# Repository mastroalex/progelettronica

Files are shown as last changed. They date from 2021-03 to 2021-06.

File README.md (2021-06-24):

# Progetto elettronica

## Introduction 
The idea of the project is to show the concept and how to control gripper and rotation via sensor signals. The structure is very simple and made in full of maker and DIY philosophy, only with recycled objects. 
An example in the following figure.

Demonstration: [https://youtu.be/k1hNBbgfAyE](https://youtu.be/k1hNBbgfAyE)

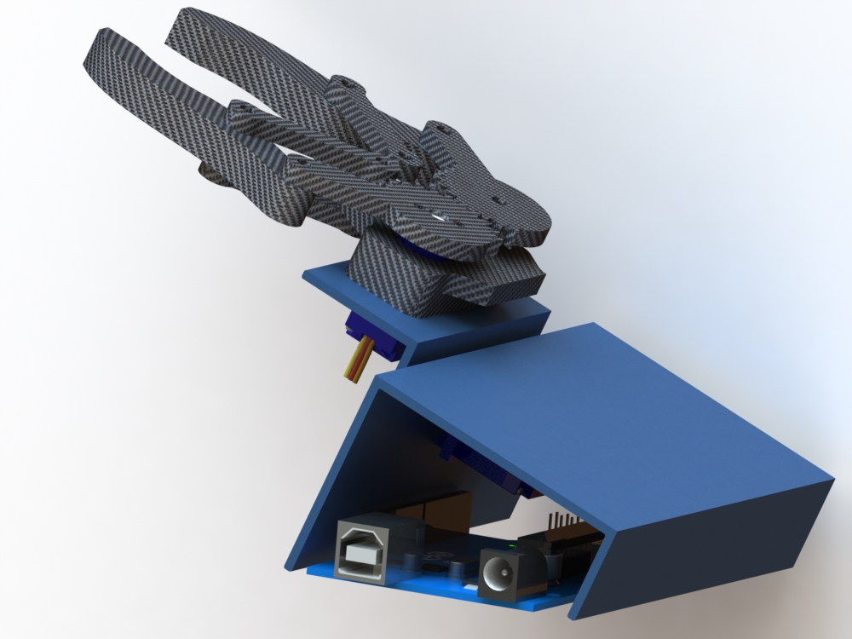
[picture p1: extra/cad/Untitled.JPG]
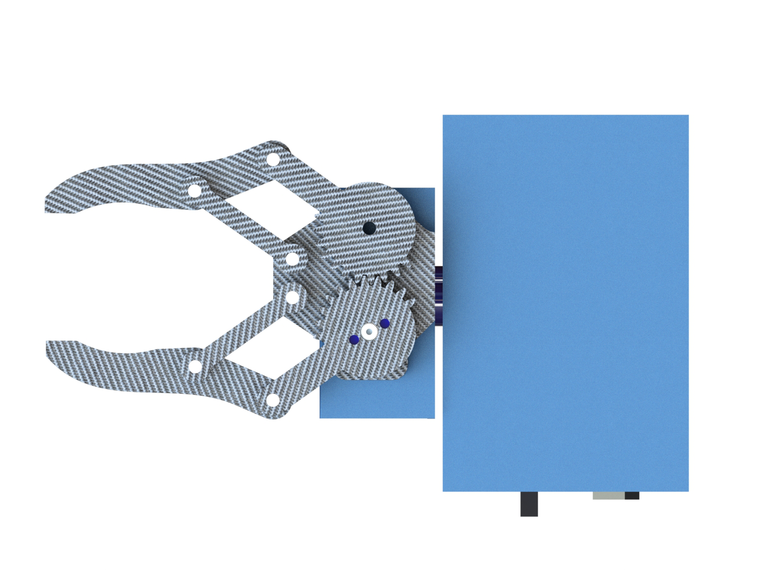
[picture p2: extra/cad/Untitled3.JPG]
  

The gripper has been further simplified in different version but the same project could be realized by purchasing a robot gripper. 

One possibility is to make it with two gears by connecting one to the servomotor. this version involves the use of recycled materials to demonstrate the use of the device.

structure 

For data charts: [bit.ly/datiprogettoelettronica](http://bit.ly/datiprogettoelettronica). 

## Table of contents
- [Progetto elettronica](#progetto-elettronica)
  * [Introduction](#introduction)
  * [Table of contents](#table-of-contents)
  * [Prerequisites](#prerequisites)
  * [Getting started](#getting-started)
    + [GY-521](#gy-521)
    + [Servo](#servo)
    + [EMG Sensor](#emg-sensor)
    + [EMG Electrodes](#emg-electrodes)
    + [Pulse sensor](#pulse-sensor)
    + [DS18B20 Sensor](#ds18b20-sensor)
    + [Sensor testing](#sensor-testing)
  * [Device division](#device-division)
    + [nRF24L01](#nrf24l01)
    + [Arduino Nano for sensing](#arduino-nano-for-sensing)
    + [Arduino Uno for execution](#arduino-uno-for-execution)
  * [GUI](#gui)
    + [Processing and computer app](#processing-and-computer-app)
    + [Python app](#python-app)
    + [Mobile app](#mobile-app)
    + [iOS App](#ios-app)
  * [Data logging and storage](#data-logging-and-storage)
    + [Esp 8266](#esp-8266)
    + [DHT 11](#dht-11)
    + [MySQL Database](#mysql-database)
    + [POST Request](#post-request)
    + [Data visualizing](#data-visualizing)
  * [Make it more compact](#make-it-more-compact)
    + [Sensors cable](#sensors-cable)
    + [Reading station](#reading-station)
    + [Power supply](#power-supply)
  * [Conclusions and future developments](#conclusions-and-future-developments)
  * [References](#references)
  * [Authors](#authors)

## Prerequisites

* Arduino UNO
* Arduino Nano
* GY-521
* EMG Sensor 
* EMG Electrodes
* Microservo motor SG90
* DS18B20 Sensor
* nRF24L01
* HC-05(06)
* ESP8266 Node Mcu
* TTL Converter 3,3-5V
* RJ45 Connectors & Cat5e cable
* LCD Display (I2C)
* Trimmer
* DHT11
_________________

* [MPU6050_tockn](https://github.com/Tockn/MPU6050_tockn) - Arduino library for easy communicating with the MPU6050
* nRF24L01 Library 
* Vectorial graphic software
* DHT Library

* MySQL server
* Web domain 

## Getting started

> Watch: [https://youtu.be/k1hNBbgfAyE](https://youtu.be/k1hNBbgfAyE)

### GY-521 
GY-521 is a module that manages the MPU-6050 sensor, a chip manufactured by Invensense, which is a IMU (Inertia Measurement Unit) sensor based on MEMS technology that contains a three-axis accelerometer and a three-axis gyroscope embedded in a single chip. This is a 6 DOF (degrees of freedom) IMU sensor so it gives six values as output. It also contains a temperature sensor.

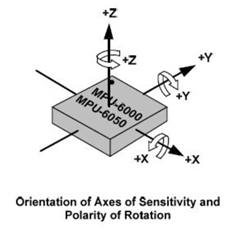
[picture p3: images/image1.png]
orientation_of_axes


The accelerometer is capable of detecting the angle of inclination along the three axes, while the gyroscope detects the angular velocity around the three axes.
GY-521 module is small in size but it is very accurate, it contains a 16-bit analog to digital conversion hardware for each channel so it captures the x, y, and z channel at the same time.
The sensor uses the I2C protocol for communication.
Two libraries are required one for the I2C and the other for communicating with MPU-6050.
 ```c
 #include <MPU6050_tockn.h>
 MPU6050 mpu6050(Wire);
 #include <Wire.h>
 ```

### Servo 
A servomotor is a rotary actuator or linear actuator that allows for precise control of angular or linear position, velocity and acceleration. It consists of a suitable motor coupled to a sensor for position feedback. It also requires a relatively sophisticated controller, often a dedicated module designed specifically for use with servomotors.

Microservo SG90 is used. It can rotate approximately 180 degrees (90 in each direction) and works just like the standard kinds but smaller.

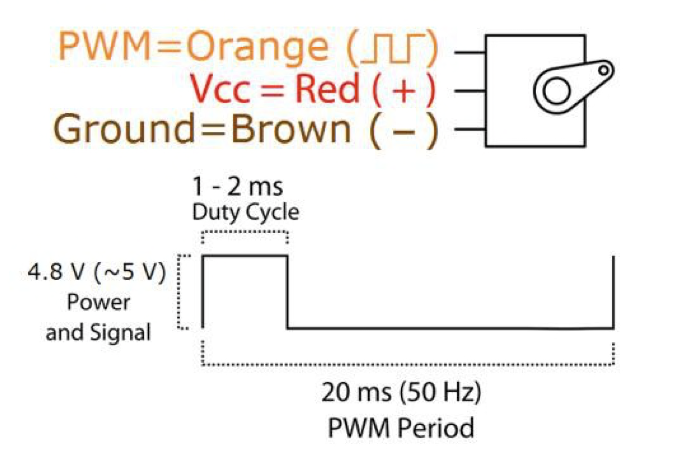
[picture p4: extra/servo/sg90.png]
servo_control


Position "0" (1.5 ms pulse) is middle, "90" (~2ms pulse) is middle, is all the way to the right, "-90" (~1ms pulse) is all the way to the left.
The Servo library is used to control the servo motor.
 ```c
#include <Servo.h> 
Servo servo-object-name;
```

Then use the following command to control angle from 0 to 180 degrees.

 ```c
servo-object-name.write(degrees);
```
The following diagram includes the connection for both the servo and the IMU.

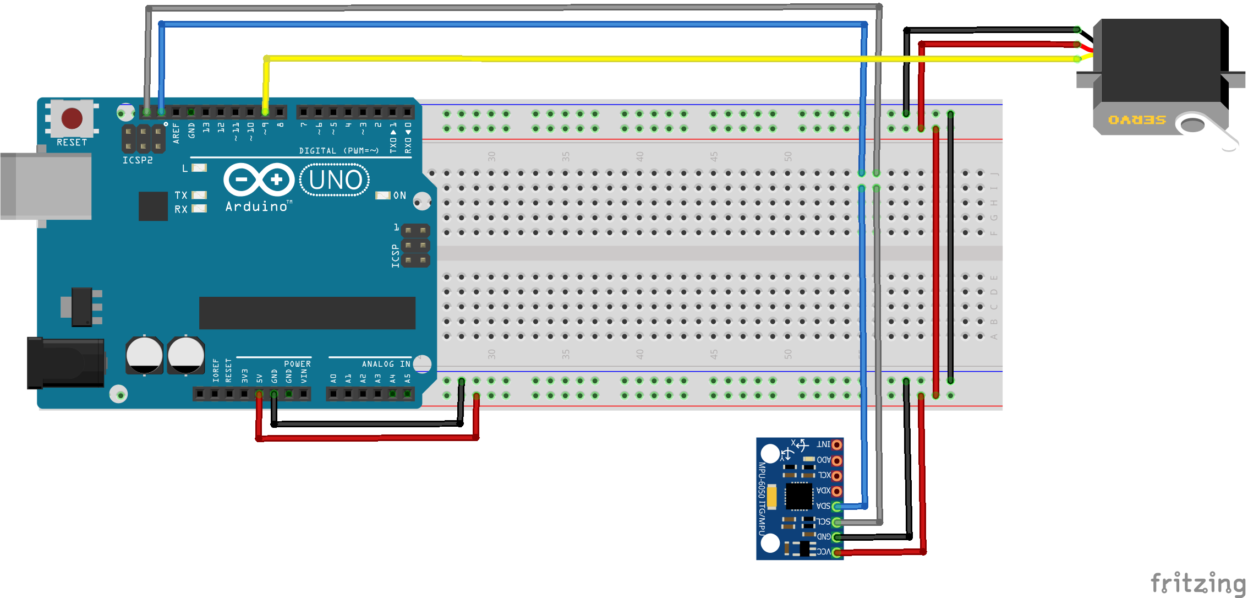
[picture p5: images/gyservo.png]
servo+gy


### EMG Sensor
EMG (Electromyography) sensor is able to measure a muscle's activity by monitoring the electric potential generated by muscle cells, electromyography has traditionally been used for medical research and diagnosis of neuromuscular disorders, however now EMG sensors are used in robotics and other control systems. It evaluates the health condition of muscles and the nerve cells that control them. These nerve cells are known as motor neurons. They transmit electrical signals that cause muscles to contract and relax. An EMG translates these signals into graphs or numbers, helping doctors to make a diagnosis.
This sensor amplifies and processes the electric activity of a muscle and converts it into an analog signal which can be read by any microcontroller with an analog-to-digital converter like Arduino.
When the muscle under test flexes, the sensors's output voltage increses.

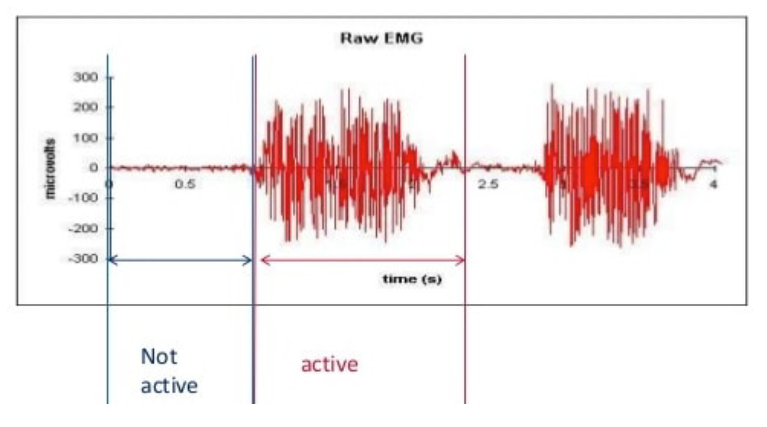
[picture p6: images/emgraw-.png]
emgraw


Linked to the sensor via 3,5 mm jack connector there is a cable which is connected on one side to Arduino, while on the other side ends with three snap connectors 
that attach to three electrodes.

Muscle Sensor v3 is used. It needs a positive and negative reference voltage so two 9V batteries are required.

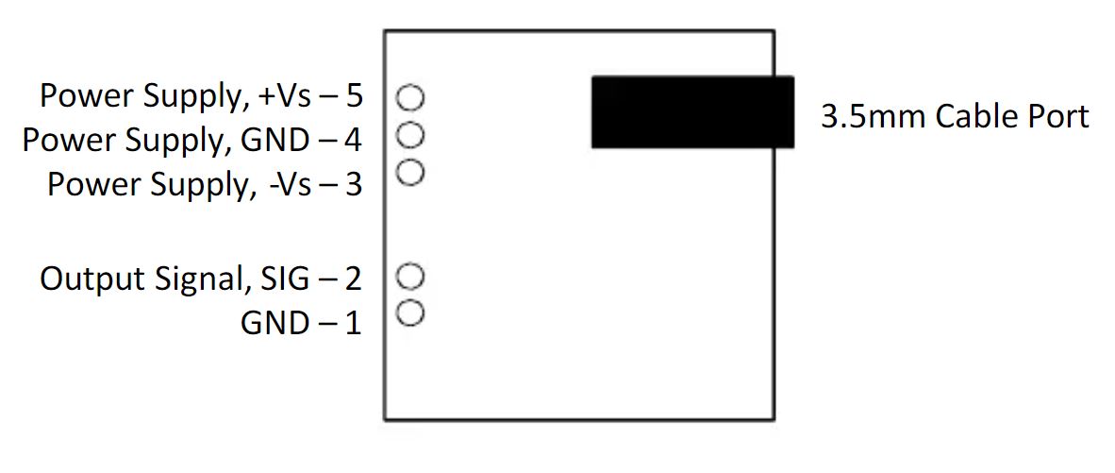
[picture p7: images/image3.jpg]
muscle_sensor


Surface EMG can be recorded by a pair of electrodes or by a more complex array of multiple
electrodes. More than one electrode is needed because EMG recordings display the potential
difference between two separate electrodes.

As you can read in the datasheet or in schematic, the two electrodes signal enter into an amplifier for instrumentation: 

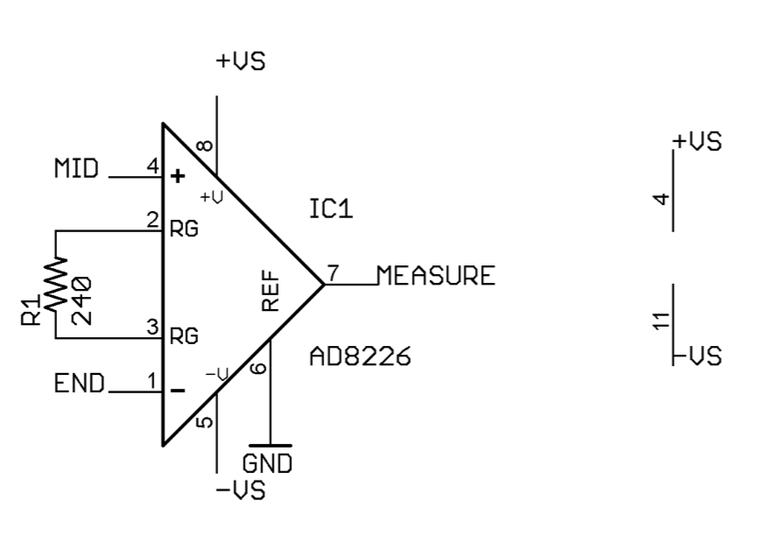
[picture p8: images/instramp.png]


Subsequently the signal is rectified:

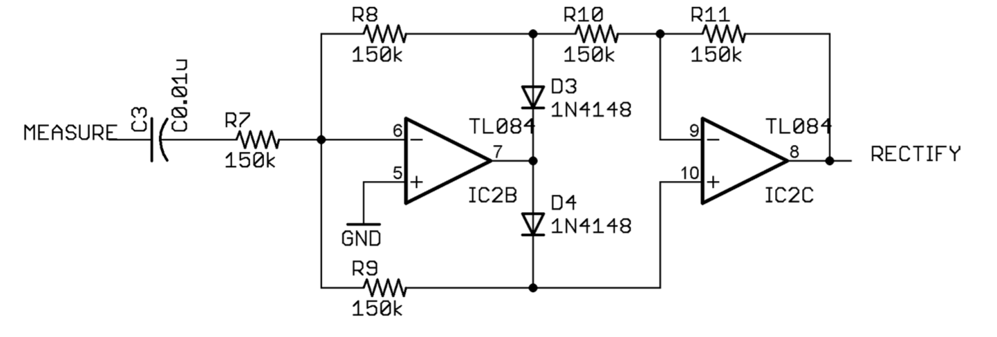
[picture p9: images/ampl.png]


And finally it is smoothed:

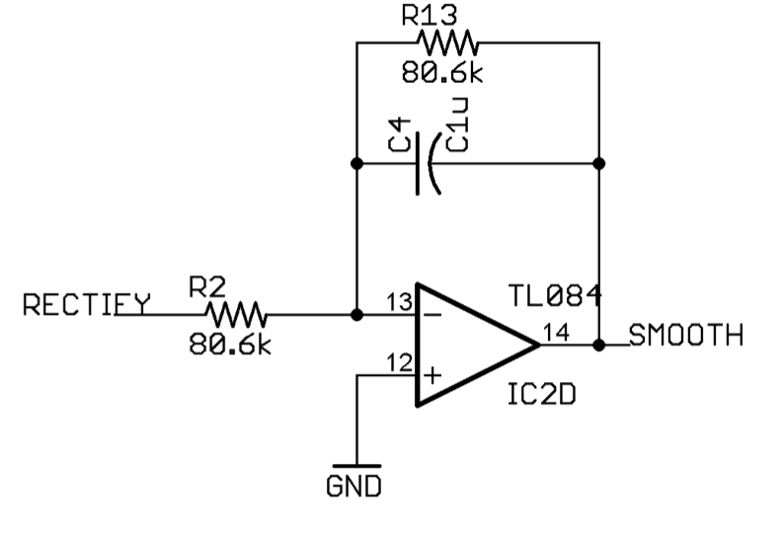
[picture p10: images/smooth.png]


In summary we will have a variable signal with muscle contraction that will be sent to the Arduino A/D converter.

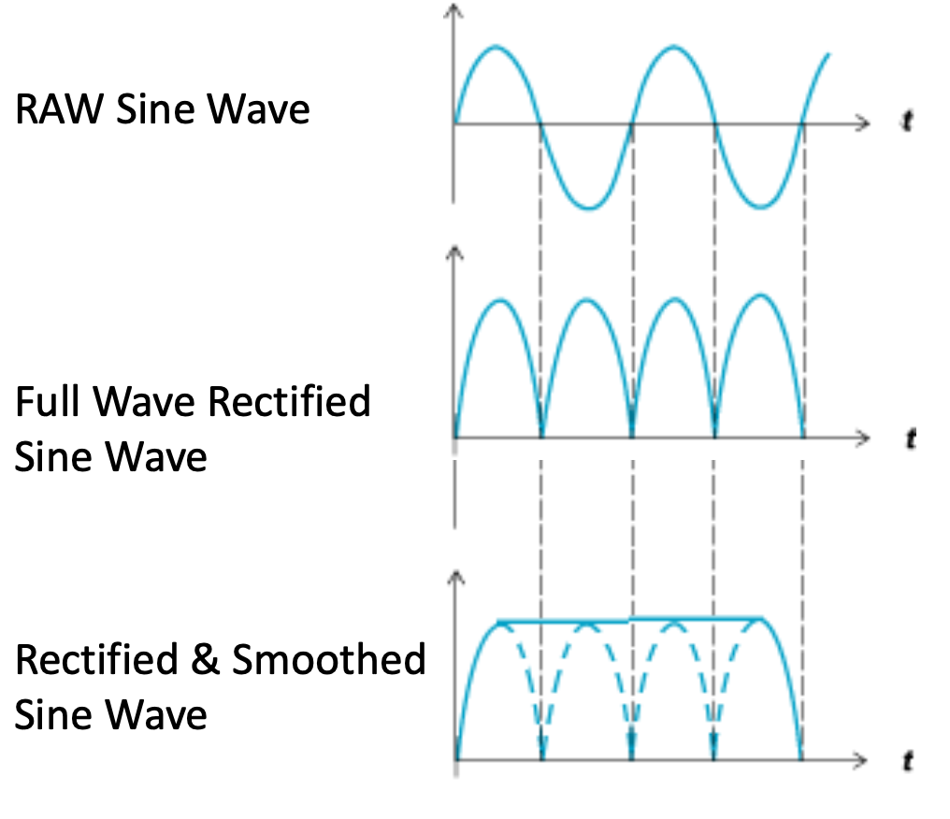
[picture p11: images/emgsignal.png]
emgsignal


The muscelsensor V3 is discontinued so we have chosen a copy. This copy of the V3 allows a considerable saving however it has some defects. This sensor outputs a signal without smoothing and full of disturbs.

We also made a vectorial copy (`.svg`) that you can include in fritzing to easily draw the following schemes. This requires respecting the [fritzing standards](https://fritzing.org/learning/tutorials/creating-custom-parts) to design own parts. For more informations [this guide](https://learn.sparkfun.com/tutorials/make-your-own-fritzing-parts/all).

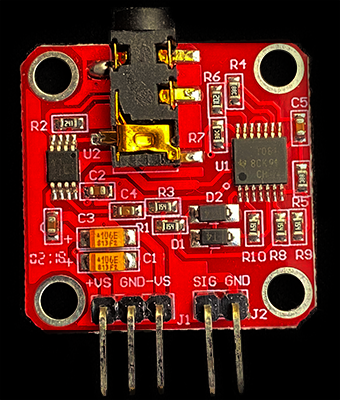
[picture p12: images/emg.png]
emg
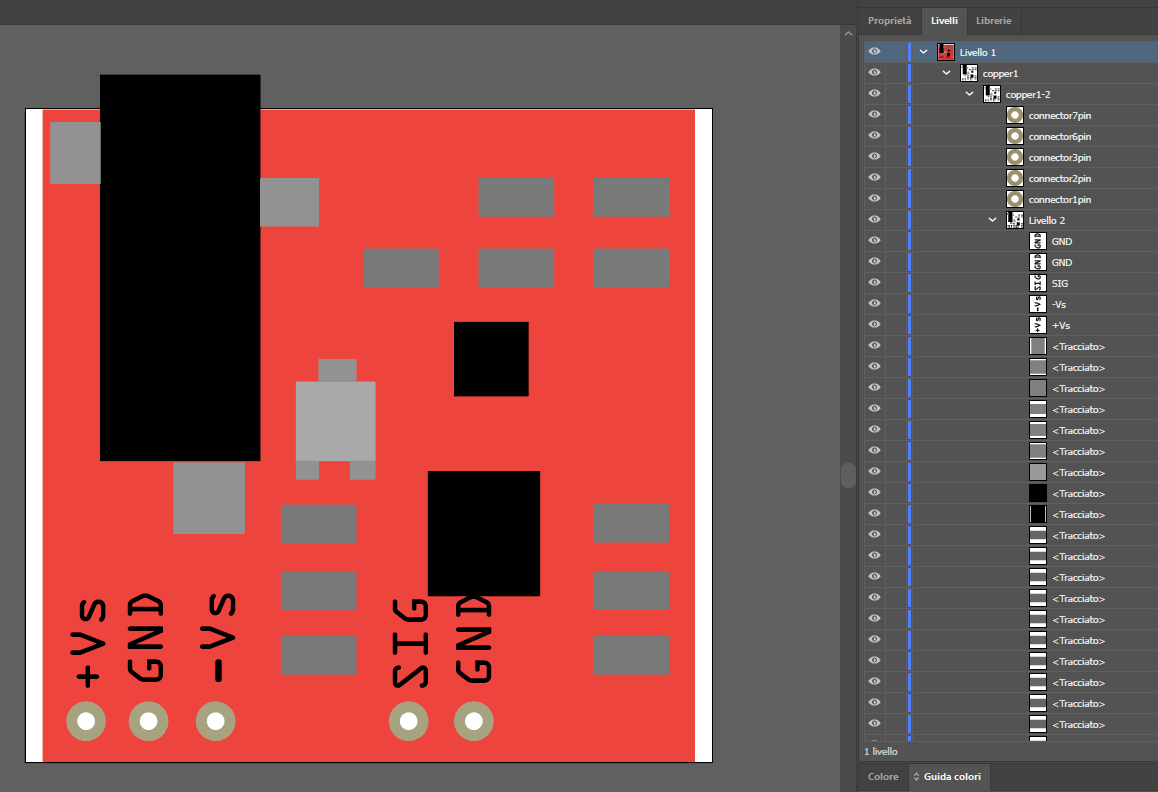
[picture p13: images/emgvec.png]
emg2
 

### EMG Electrodes
The electrical activity of a muscle is detected with the help of EMG electrodes. There are differente types of electrodes, surface EMG electrodes are used in this project, in particular the gelled one.
This type of elecrodes contains a gelled electrolytic substance as interface between electrodes and skin. 
Gelled EMG electrodes provide a non invasive technique for measurements and detection of EMG signal, but they are generally used for superficial muscles since they are applied on the skin. 
The EMG electrodes must be positioned appropriately. In particular two EMG electrodes should be placed between the motor unit and the tendinous insertion of the muscle, along the longitudinal midline of the muscle. The distance between the center of the two electrodes should be 1-2 cm. Red snap connector in the middle of muscle body and the green one at one end of the muscle body. 
The third electrode (yellow one) must be placed on an inactive section of the body.

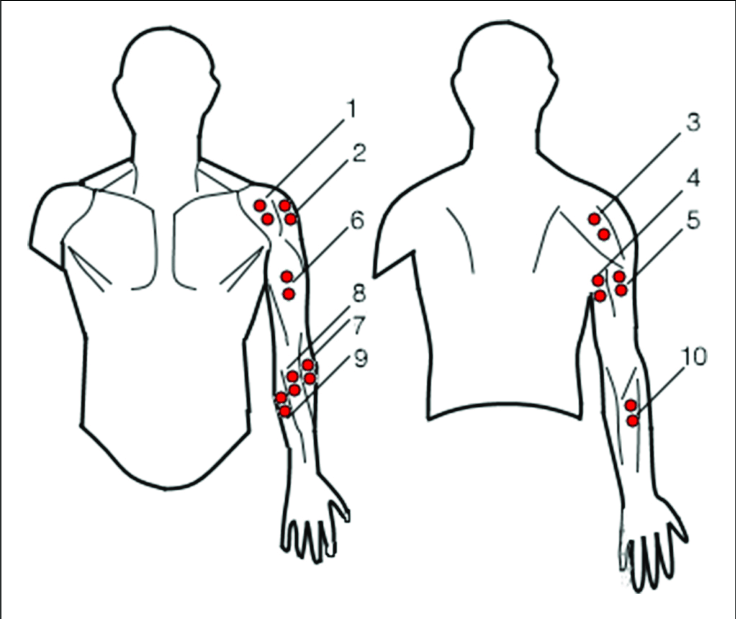
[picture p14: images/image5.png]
electrodes_placement


It is also important to do some considerations about emg signals.

The electrical source is the muscle membrane potential of about –90 mV. 
Typical repetition rate of muscle motor unit firing is about 7–20 Hz, depending on the size of the muscle
Measured EMG potentials range between less than 50 μV and up to 30 mV, depending on the muscle under observation. 
**It must be amplified !**

Due to the low quality of the emg circuit the analog signal was full of noise. The voltage was only rectified but not very leveled. So we provided to simple smoothing algorithm.

```c

int readings[numReadings];      // the readings from the analog input
int readIndex = 0;              // the index of the current reading
int total = 0;                  // the running total
int average = 0;                // the average
int inputPin = A0;              // EMG analog pin

void setup() {
    Serial.begin(9600);
  // initialize all the readings to 0:
  for (int thisReading = 0; thisReading < numReadings; thisReading++) {
    readings[thisReading] = 0;
  }
}

void loop() {
 
  total = total - readings[readIndex];          // subtract the last reading:
  readings[readIndex] = analogRead(inputPin);   // read from the sensor
  total = total + readings[readIndex];          // add the reading to the total:
  readIndex = readIndex + 1;                    // advance to the next position in the array:

  if (readIndex >= numReadings) {               // if we're at the end of the array
    readIndex = 0;                              // wrap around to the beginning
  }
  average = total / numReadings;                // calculate the average:
                                                // print different data for plotting
  Serial.print(average);
  Serial.print("\t");
  Serial.print(soglia);
  Serial.print("\t");
  Serial.println(analogRead(inputPin));
  delay(1);                                     // delay in between reads for stability
}
 ```

 This is the [Arduino's reference smoothing scritp](https://www.arduino.cc/en/Tutorial/BuiltInExamples/Smoothing/) with little changes made after a long period of testing.

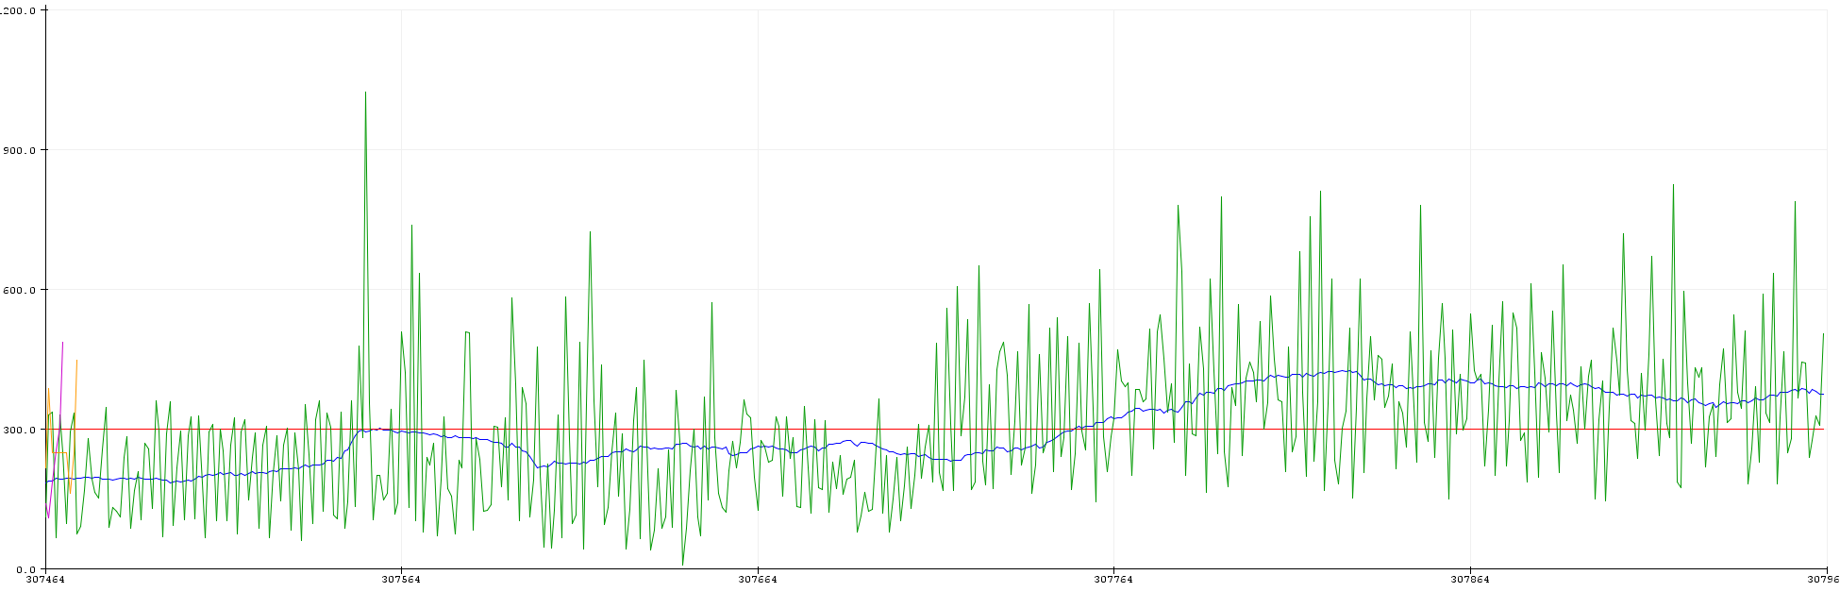
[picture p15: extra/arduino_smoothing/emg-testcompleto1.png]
smoothing
 

 > Smoothed signal (blue), original signal (green), threeshold (red). When the signal is below the threshold the arm is relaxed otherwise it is contracted.

 This smoothed `average` allows us to customize the following control code for the clamp servo.

 ```c
#include <Servo.h>
Servo servoclamp;
long t3 = 0;
long t4 = 20;
boolean controllo[10];
boolean stato;
int i = 0;
int soglia = 350; // Threeshold
// This value derives from a long period of testing. 
// You will need to do several tests 
void setup() {
  servoclamp.attach(5);
    // other code...
  }
 void loop() {
// other code..
  if (average > soglia) {
    servoclamp.write(max_servo_angle);// gripper closing
  }
  if (millis() - t3 < t4) {
    if (average < soglia) {
      controllo[i] = LOW;
    }
    else {
      controllo[i] = HIGH;
    }
    if (i < 10) {
      i++;
    }
    t3 = millis();
  }
    // only if the average is below the threshold
    // for a long time is it possible to close the clamp 
    // this allows to avoid problems due to sudden oscillations of the signal
  for (int j = 0; j < 10; j++) {      
    if (controllo[j] == LOW) {      
      stato = LOW;
    }
    else {
      stato = HIGH;
    }
  }
  if (stato == LOW) {
    servoclamp.write(min_servo_angle);   // gripper opening
  }
 }
 ```

### Pulse sensor 

The principle is to make a light shine between your fingers. Most of the light is absorbed or reflected, but some light will pass through our tissues if they are thin enough. When blood is pumped through your body, it gets squeezed into the capillary tissues, and the volume of those tissues increases very slightly. Then, between heart beats, the volume decreases. The change in volume effects the amount of light that will transmit through. This fluctuation is very small, but we can sense it with electronics. Here's how it's done.

We start with a light source and a light detector. Using an Infrared LED, and a photodiode sensor. It's important that the two devices are matched well, so that the light wavelength output from the LED is detected strongly by the photodiode (see below for part numbers). The photodiode is essentially a teeny tiny solar cell, just like the panels on rooftops, but really small. It will generate a small voltage and current when it is blasted with photons. The Infrared LED is what we will use for our photon blaster.

The next thing we need is a way to amplify the tiny signal coming off of the photodiode. Happily enough, the configuration of this circuit is well-known  as a 'Current to Voltage Converter' and it is a classic.

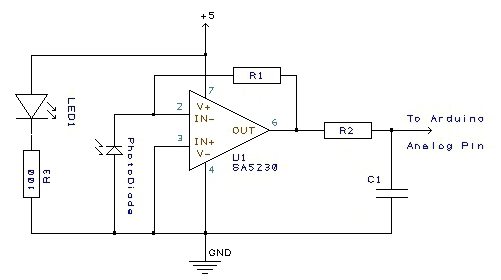
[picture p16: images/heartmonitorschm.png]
heartmonitorschm


The photodiode needs to be shielded from ambient light, which generates alot of noise in the signal. 
The waveform here is usable, but as you can see, the pulse signal is distorted by even small movements. Also any misalignment or movement of the IR LED will muddy up the signal.

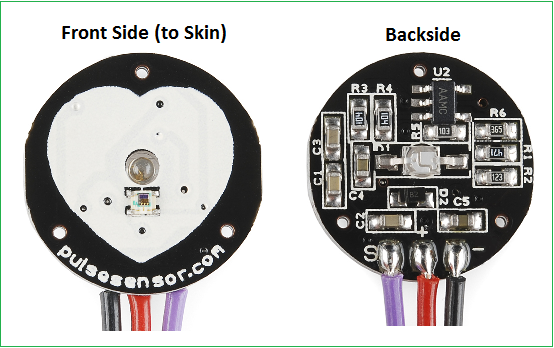
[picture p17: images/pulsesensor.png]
pulse


pulsesensor.com make a Pulse Sensor that is small enough to be worn comfortably in many configurations, and immune to signal noise generated by moving around, or changes in ambient lighting conditions.
They found a super small integrated circuit that has an on-board photodiode and op amp circuit combined. The super smallness means that we can maintain close, steady contact with the skin. This shields the sensor from changes in ambient light and makes noise from moving around minimal at most. 

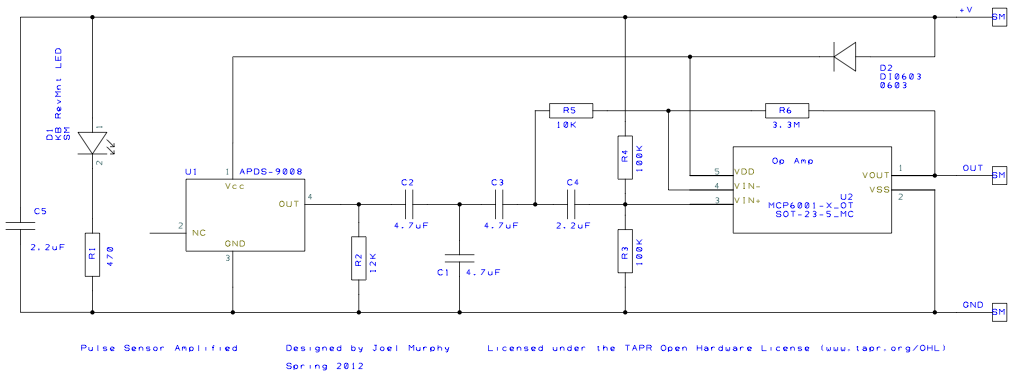
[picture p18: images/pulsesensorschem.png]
pulsesensorschem


The raw signal looks like:

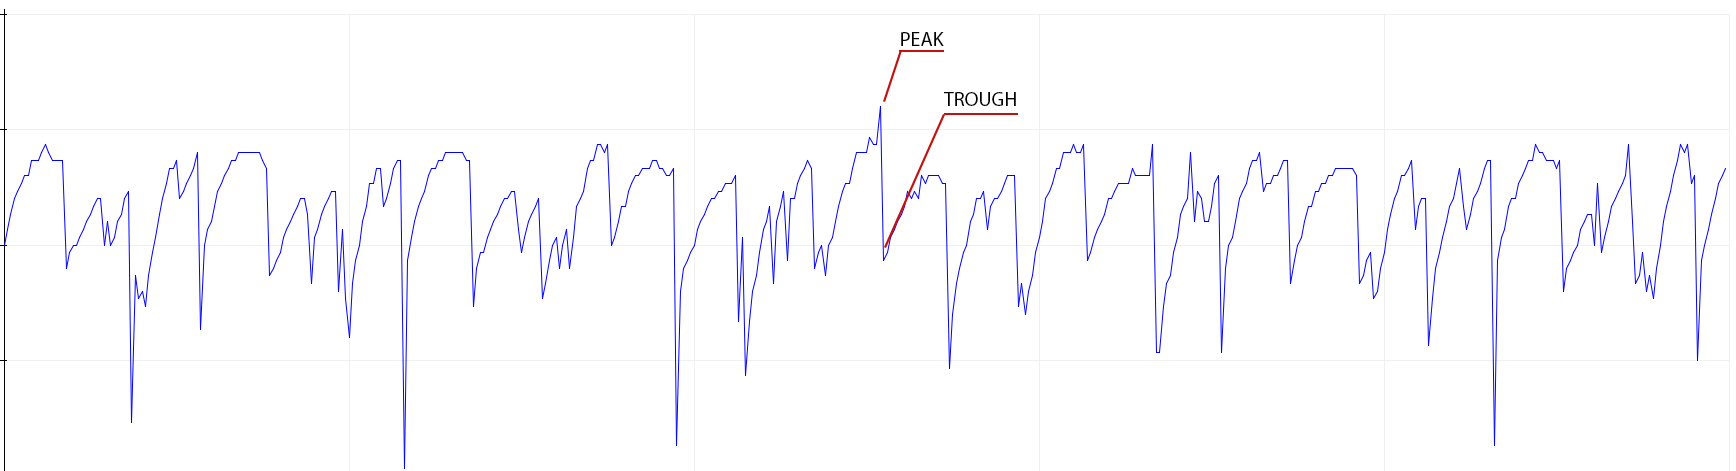
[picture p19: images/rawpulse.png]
rawpulse


A first possibility is to use the library provided `PulseSensor Playground` , however this is not fully compatible with the other features we want to implement. So we proceeded to write a special code. 

Reading is callback by `battiti()` function described in the library `funzioniBPM.h`.

We have therefore put together several ideas from [instructables.com](https://www.instructables.com/circuits/howto/pulse+sensor/) and from [pulsesensor.com](https://github.com/WorldFamousElectronics/PulseSensor_Amped_Arduino/blob/master/PulseSensorAmped_Arduino_1.5.0/PulseSensorAmped_Arduino_1.5.0.ino) to obtain a code that takes care of reading the analog value and identifying the beat above a certain threshold. The code is relatively complex. 
Besides a part to print symbols or an affirmative sentence when the beat is actually detected.
Timer 2 is used to set an interrupt every 2 ms. a more complex piece of code takes care of measuring the time elapsed since the last beat and making appropriate samples to avoid noise. In particular, an attempt is made to avoid dichrotic noise and to reveal peaks. When a beat is detected (peak in compliance with the imposed conditions) the time value is updated and the BPM is calculated as well as the number of beats that can occur in 1 minute (60000 ms).

The main functions are performed by `ISR(TIMER2_COMPA_vect)` and `battiti()` and `serialOutputWhenBeatHappens()` take care of returning the beat values. 

### DS18B20 Sensor
DS18B20 is a digital temperature sensor, which is a sensor capable of measuring the temperature of the environment but also of the ground or to detect temperature in liquids. 
This sensor is available in several sizes, in this project it has been used the one inserted into a waterproof probe. The DS18B20 sensor is much more sensitive than the DHT11 
(temperature and humidity sensor) because it can reach 9 to 12 bit resolution. More with this module it is possibile to add multiple sensors on the same bus, each 
DS18B20 has a unique 64-bit serial code, which allows multiple DS18B20s to function on the same bus.
The protocol used is OneWire protocol which uses a digital pin, from which a bus starts and allows us to communicate with a specific device on the bus knowing the address.

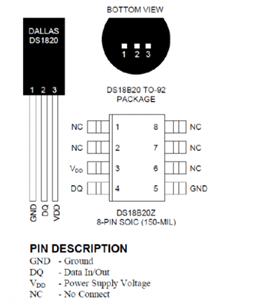
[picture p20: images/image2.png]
temperature_sensor


Two libraries are required, the first one is the DallasTemperature and the second one is the OneWire library. 

 ```c
#include <DallasTemperature.h>
#include <OneWire.h>
```

The DS18B20 was then discontinued due to an incompatibility of the library interrupts and the other functions. The temperature of the GY-521 was deemed to be sufficiently accurate.

### Sensor testing 

The following circuit shows the test setup for developing the initial code:

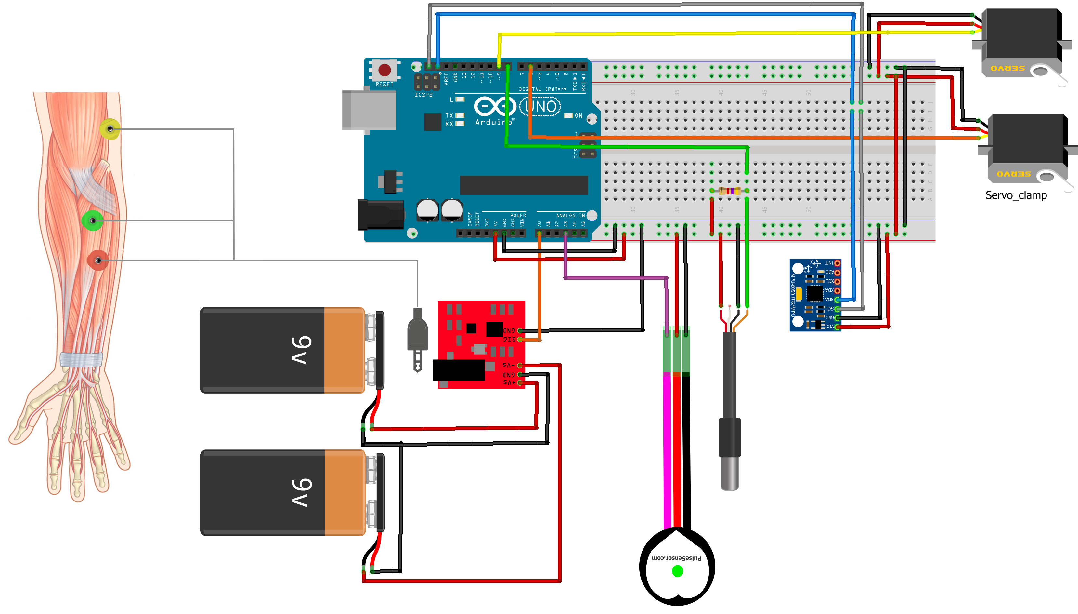
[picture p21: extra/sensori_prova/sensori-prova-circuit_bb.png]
sensor_testing


This configuration of two 9V DC power supplies allows you to have +9 and -9 on the Vs terminals.
It is also possible to use 18V DC power supply and split it in +9V and -9V.

This configuration allowed us to do all the device and code tests. We therefore reworked part of the code by dividing it into the various modules in order to have a more modular system that would allow you to add or remove devices as needed.
From this configuration we started to divide then into a structure determined for monitoring and a structure with actuators.

In the end the sensors that must arrive on the wrist will be joined in a single cable equipped with a connector to connect it to the monitoring structure. 

Everything will be reorganized in a more compact way

## Device division

At this point we have divided the code and the devices. We use an arduino nano to read the sensors and an arduino uno to control the servo motors.

Communication between the two is via radio using two NRF24L01 Single chip 2.4 GHz Transceiver.

### nRF24L01

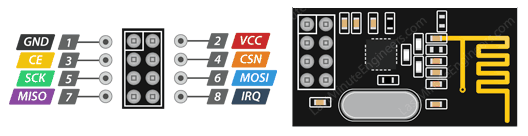
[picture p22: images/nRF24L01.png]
nrf24


The device has an operating voltage of 1.9V ~ 3.6V, a built-in 2,4GHZ antenna and an operating speed (max) of 2 Mbps. 
The chip is managed by the SPI interface. Through this interface it is possible to access the registers of the chip and modify all its parameters.

This complex operation, however, is facilitated for us by libraries.

```c
#include <SPI.h>
#include <nRF24L01.h>
#include <RF24.h>
```

The connection requires several pins:
	
- GND
- Vcc, powers the module  using 3.3V
- CE, Chip Enable, used to enable SPI communication
- CSN, Ship Select Not, pin has to be kept high always, else it will disable the SPI
- SCK,Serial Clock, provides the clock pulse using which the SPI communication works
- MOSI. Master Out Slave In, Connected to MOSI pin of Arduino, for the module to receive data from the arduino
- MISO, Master In Slave Out,Connected to MISO pin of Arduino, for the module to send data from the Arduino
- IRQ, it is an active low pin and is used only if interrupt is required

To use the chip it is necessary to set reading or writing in `setup()`like:

```c
  radio.begin();
  radio.openWritingPipe(address); //for receiving 
//radio.openWritingPipe(address); // for trasmitting
  radio.setPALevel(RF24_PA_MIN);
  radio.stopListening(); //for receiving 
//radio.stopListening();// for trasmitting
```

It is also important to define Chip Enable `CE`and Ship Select Not `CSN`

For the transmission we used a function `charfortransmission()` created ad hoc that allows to concatenate a letter which indicates which data we are transmitting and the value assumed from the corresponding variable. this function is cycled in the `loop()` and continuously called by sending it different parameters depending on the variable. It is then converted into `char` to allow correct transmission with the libraries it uses. 
The receiver has a similar function `radionuovo()` that first analyzes the first character identifying what information is received and then enters the data in the variables of interest, after making the appropriate variable type conversions

### Arduino Nano for sensing 

> Configuration with Arduino nano and sensors on breadboard for testing

nanosensor

For the arduino dedicated to sensors, the circuit has been modified by adding an LCD display to monitor the parameters and an nRF24L01 for radio transmission. The LCD display is connected with an I2C interface module to simplify communication and cable management. The connection of the sensors has remained the same. The DS18B20 sensor has been temporarily excluded due to incompatibility between the libraries. We will decide later whether to include it again by changing the code. So the temperature of the GY-512 is used although not as accurate.

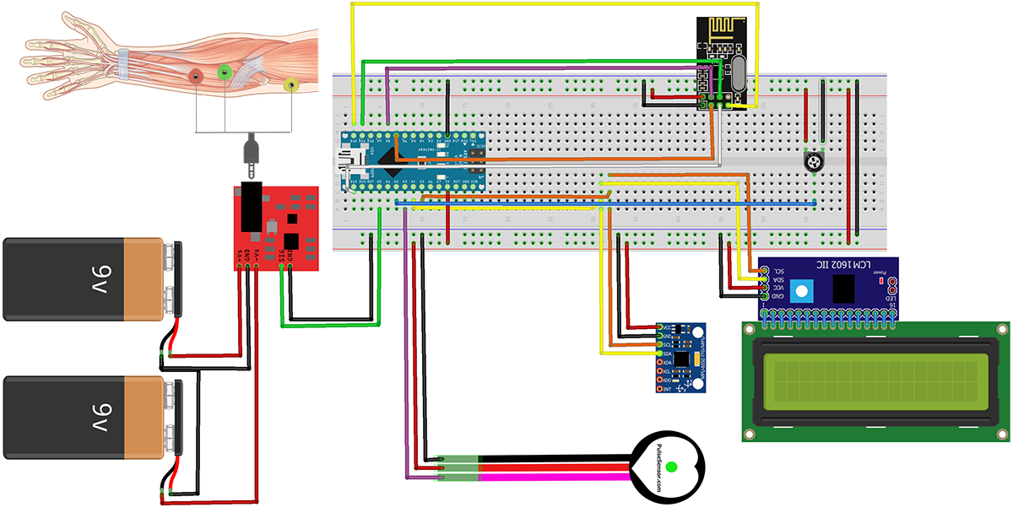
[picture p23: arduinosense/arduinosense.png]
arduinosense


An arduino nano was used to make the whole thing more compact. The pin definition remains the same. It is important to remember that there are no dedicated SDa and SCL pins but they are on A4 and A5.

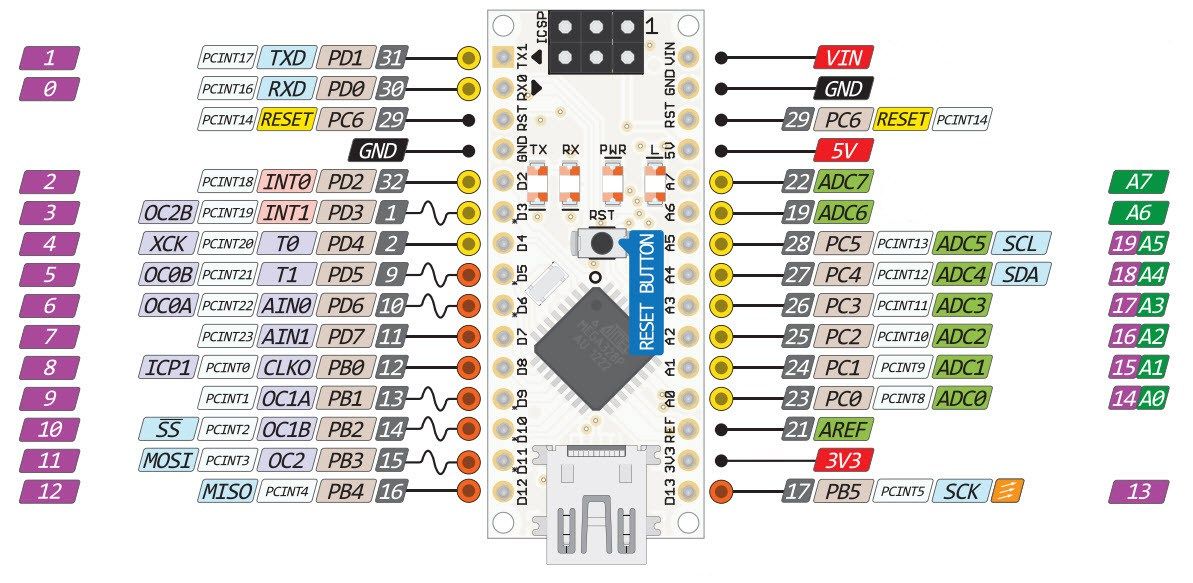
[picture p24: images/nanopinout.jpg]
nanopinout


In the code the elements related to the servo motors have been removed and the rest has been rearranged.

The main code is as follows:

```c
#include <MPU6050_tockn.h>
#include <Wire.h>
#include "funzioniBPM.h" // battiti
#include "printerfunzioni.h" // stampante
#include "EMGsmooth.h" // lettura emg
MPU6050 mpu6050(Wire);
void setup() {
  Serial.begin(9600);
  Wire.begin(); // avvio e inizializzo il gyro
  mpu6050.begin();
  mpu6050.calcGyroOffsets(true);
  // mpu6050.setGyroOffsets(0, 0, 0);
  for (int thisReading = 0; thisReading < numReadings; thisReading++) {  // initialize all the readings to 0:
    readings[thisReading] = 0;
  }
  t1 = millis();
  interruptSetup();                 // sets up to read Pulse Sensor signal every 2mS
  lcd.begin(); // initialize the LCD
  lcd.backlight();
}
void loop() {
  average = averagecalc (); // calcolo media EMG
  mpu6050.update();
  tempmpu = mpu6050.getTemp(); // prende la temperatura
  angle = mpu6050.getAngleX(); // prende l'angolo lungo x
  printatore(LOW); // set HIGH to debug EMG with serial plotter
  lcdprint();
  battiti();
  charfortransmission("T", String(tempmpu));
  charfortransmission("A", String(angle));
  charfortransmission("M", String(average));
  charfortransmission("B", String(BPM));
  charfortransmission("S", String(soglia));
  delay(1);
}
```

This main code has been simplified by adding several functions that call external library definitions:
- ` averagecalc() ` has been defined in the `EMGsmooth.h` and is used to calculate the average of the distorted EMG signal
- `printatore(LOW)` it is a special function that can be used to print the EMG signal for the serial plotter in order to debug any problems with the detection. It is usually used to print all values on the serial monitor. It is defined in `printerfunzioni.h`
- `lcdprint()` it is used to print the different values and connected symbols on the LCD display
- `battiti()`it is used to reveal heartbeats and BPM. It has been defined in the `funzioniBPM.h`
- `charfotransmission()`to trasmitting data with relative informations

To maintain the code clear this function was defined in external libraries. 
The `EMGsmooth.h` library it's responsible of smoothing emg signal in order to obtain precision in threshold determination.
The `funzioniBPM.h` library has already been described in the pulse sensor paragraph.
The `printerfunzioni.h` contains the function to print in the serial monitor and in the lcd display. It also contains the definition of the LCD symbol as an arrow or heart.

To create special characters for LCD it is used  [LCD Custom Generator](https://maxpromer.github.io/LCD-Character-Creator/) that allow us to generate a byte custom char with pixel ON/OFF definition. This allows us to use special symbols in addition to ASCII characters by individually defining the on and off pixels in an 5x8 matrix (`byte_matrix`). It is possible to create up to 8 different symbols with the `createChar ()` function of the LiquidCrystal library and print them with `lcd.Write()`. For example for heart symbol:

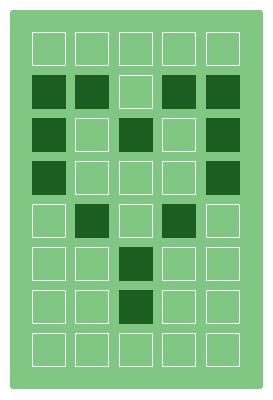
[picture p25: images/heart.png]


```
byte heart[] = {
  B00000,
  B11011,
  B10101,
  B10001,
  B01010,
  B00100,
  B00100,
  B00000
};
lcd.createChar(1, heart);
lcd.setCursor(6, 0);
lcd.write(1);
```

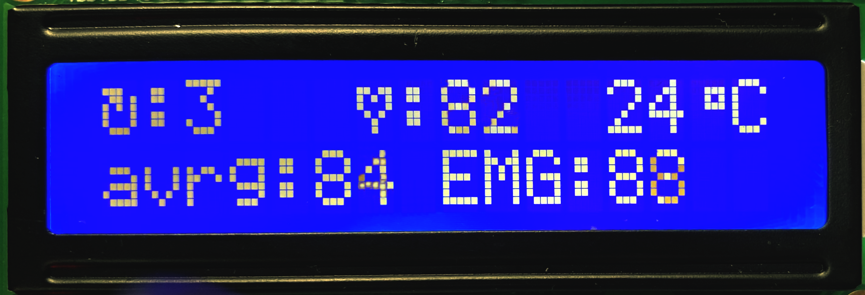
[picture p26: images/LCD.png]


Each library contains all the variables and all the other libraries necessary for their operation. 

We are therefore able to obtain the following values which must be contained to the arduino with the actuators:

- `tempmpu`
- `angle`
- `average`
- `BPM`
- `soglia`

Finally, a trimmer was also added to manually adjust the threshold on the analog pin A2.

### Arduino Uno for execution

> Configuration with Arduino Uno, servomotors, radio trasmitter and clamp  for testing

actuator

This second structure takes care of receiving the radio signals and retransmitting them via bluetooth (or via serial) and to move the two servomotors.
It is important to note that a logic level converter (3.3V 5V TTL) was used to add the bluetooth module.

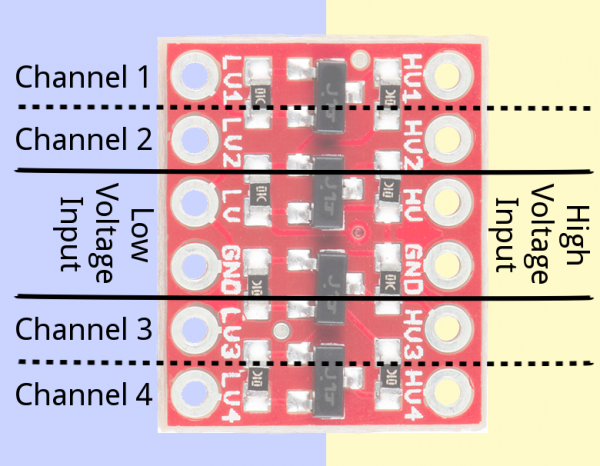
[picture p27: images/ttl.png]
ttl


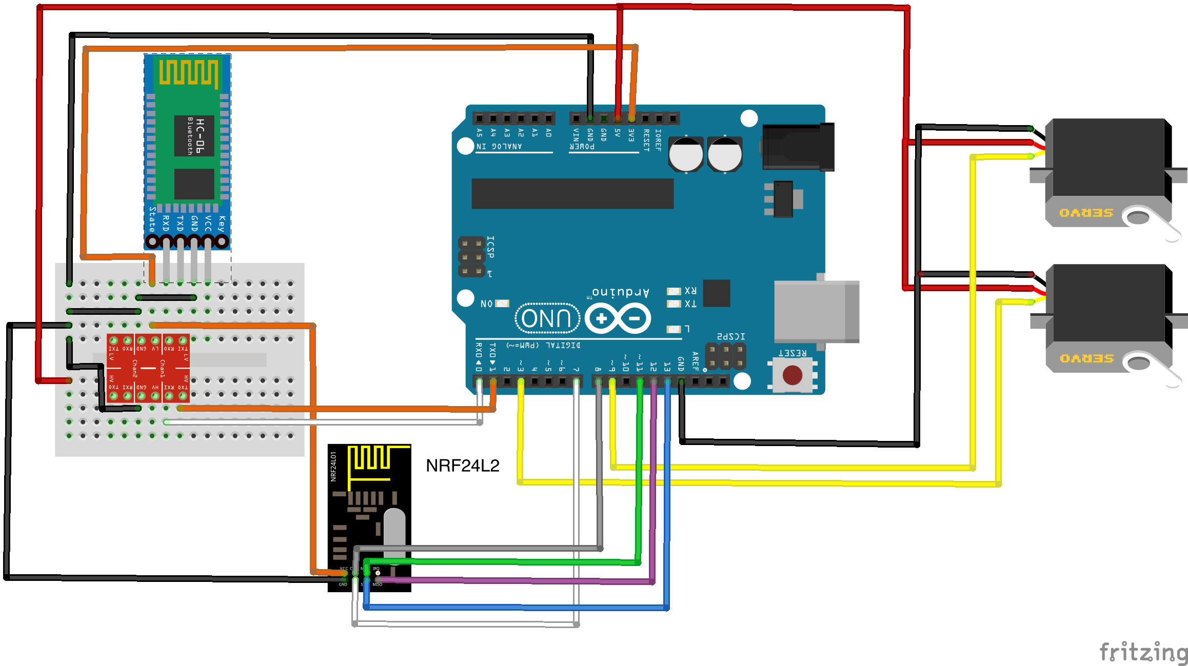
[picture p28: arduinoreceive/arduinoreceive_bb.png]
arduinoreceive


#### HC-06 for bluetooth

The hc-06 module is a device that allows you to transform a signal on the serial bus into a bluetooth signal. 

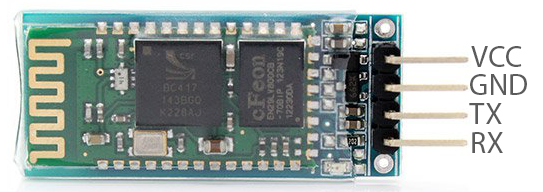
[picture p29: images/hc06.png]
hc06


Typically is used a software serial protocol to communicate however we use directly the UART bus on pin tx and rx.
So we created two new functions `radioperbt()` and `decodeserial()`.
The first one analyzes the char received from the nRF24 and according to the first letter updates the respective variable and at the same time prints the value encoded in the serial (so also in bluetooth).
The second one instead deals with analyzing the commands received. Therefore whether manual control is active or not and, if necessary, the rotation angles of the servomotors. It will be better described in the GUI section.

`radioperbt ()` was originally written as a function to decode the radio message and update variables (`radionuov ()`). Then it has been updated in order to allow bluetooth communication by sending the message encoded with the first letter that indicates which variable corresponds to the data.
```c
if (text[0] == 'T') {
      Serial.print("T");
      valore = "";
      for (int i = 1; i < 32; i++) {
        valore = valore + String(text[i]);
      }
      tempmpu = valore.toFloat();
      Serial.println(tempmpu);
    }
```
The logic is to receive an `array chart`, analyze the first char and convert all the others to the variable of interest (`float` or `int`) and print the message again as a encoded `String`.

#### Servo motors

Two functions have been created to control the servomotors.

`pos_servo()` to which we pass the inclination and takes care of remapping it correctly to rotate the structure.

`pinzacontrol()` which takes care of deciding whether or not to close the clamp according to the threshold value. There is a further check before reopening the clamp to avoid problems due to signal fluctuations.
```c
if (average > soglia) {
    servopinza.write(pinzamax);// chiudo la pinza
  }
if (millis() - t3 > t4) {
  if (average < soglia) {
    controllo[i] = LOW;
  }
  else {
    controllo[i] = HIGH;
  }
  if (i < 10) {
    i++;
  }
  t3 = millis();
  }
for (int j = 0; j < 10; j++) {
  if (controllo[j] == LOW) {
    stato = LOW;
  }
  else {
    stato = HIGH;
  }
}
if (stato == LOW) {
  servopinza.write(pinzamin);// apriamo la pinza
}
  
```

## GUI

We also found it useful to develop a graphical user interface that allow you to view data or take control of the clamp, both from a computer and from a smartphone.

### Processing and computer app

To develop computer app we use Processing, compatible with MacOs, Windows and Linux.

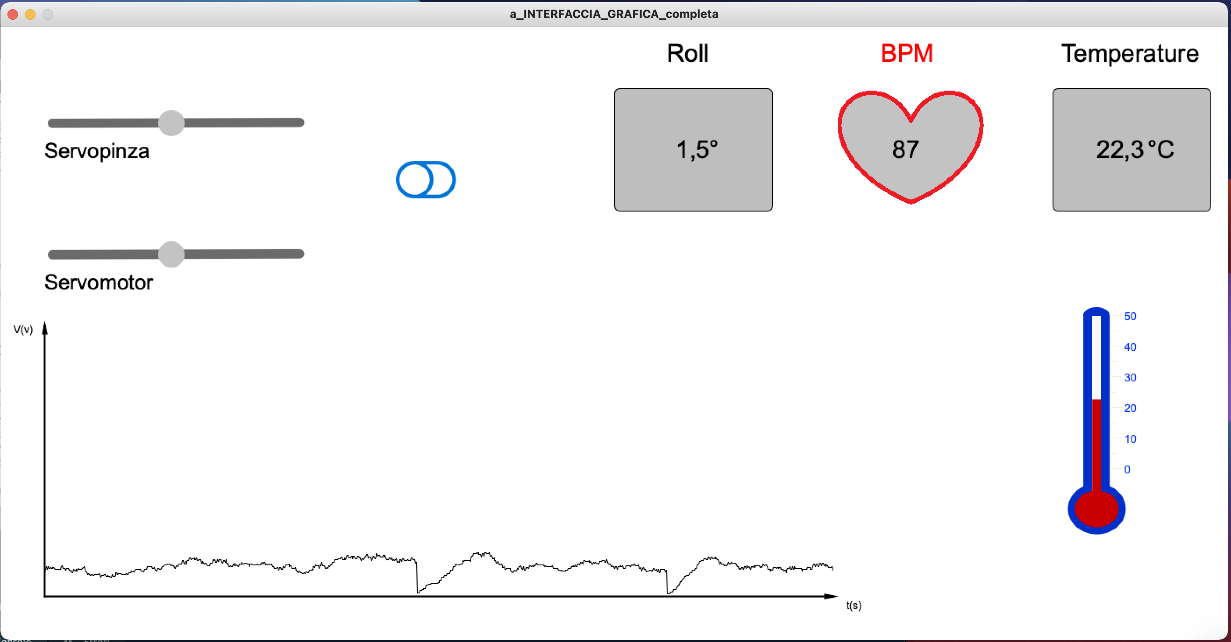
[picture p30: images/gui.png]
gui


#### Sliders

In order to control the clamp and the other servo used in this project two sliders have been created on Processing. 
The first sketch created was the one on Arduino, in particular we have used a library which is called Firmata. Firmata is a library that implements the Firmata protocol for standard communication, to make Arduino or more generally a hardware device communicate with various types of peripherals or programs. 
In this project it was used to make Arduino at the service of an external software that is Processing itself. 
In the example section of the Arduino IDE we called ServoFrimata which is one of the example programs that supports as many servos as possible using the Servo library. 
Once the example was opened, it was compiled and uploaded to Arduino. This meant that Arduino could be interfaced by using this comunication protocol with any other software, program o device with the same protocol like Processing.

The code is as follows:

```c
#include <Servo.h>
#include <Firmata.h>

Servo servos[MAX_SERVOS];
byte servoPinMap[TOTAL_PINS];
byte servoCount = 0;

void analogWriteCallback(byte pin, int value)
{
  if (IS_PIN_DIGITAL(pin)) {
    servos[servoPinMap[pin]].write(value);
  }
}

void systemResetCallback()
{
  servoCount = 0;
}

void setup()
{
  byte pin;
  Firmata.setFirmwareVersion(FIRMATA_FIRMWARE_MAJOR_VERSION, FIRMATA_FIRMWARE_MINOR_VERSION);
  Firmata.attach(ANALOG_MESSAGE, analogWriteCallback);
  Firmata.attach(SYSTEM_RESET, systemResetCallback);
  Firmata.begin(9600);
  systemResetCallback();
  // attach servos from first digital pin up to max number of
  // servos supported for the board
  for (pin = 0; pin < TOTAL_PINS; pin++) {
    if (IS_PIN_DIGITAL(pin)) {
      if (servoCount < MAX_SERVOS) {
        servoPinMap[pin] = servoCount;
        servos[servoPinMap[pin]].attach(PIN_TO_DIGITAL(pin));
        servoCount++;
      }
    }
  }
}

void loop()
{
  while (Firmata.available())
    Firmata.processInput();
}
```

In order to use the Firmata protocol on Processing, besides the serial library which is present by default on Arduino, it is necessary to import a library provided by Arduino which includes an Arduino equivalent software object, which represents the physical arduino connected via USB cable to the computer.

```js
import processing.serial.*;
import cc.arduino.*;
Arduino arduino;
Serial serial;
```

No dedicated libraries have been loaded to create the sliders. In fact the elements that create the slider have been drawn with another program and then added as images inside the program folder.

The images were then loaded into the code in this way:

```js
  barra1 = loadImage("barra1.png");
  indicatore1 = loadImage("indicatore1.png");
  barra2 = loadImage("barra2.png");
  indicatore2 = loadImage("indicatore2.png");
```
And than the images were placed on the window:

```js
  image(barra1, x1, y1);
  image(indicatore1, x2, y2);
  image(barra2, x1, y3);
  image(indicatore2, x4, y4);
```

So when the mouse moves along the x coordinate for the length of the slider in the upper half of the graphic window, the symbol which represents the indicator, will follow the mouse simulating the function of the slider. 
While when the muose moves along the x coordinate for the lenght of the slidere in the lower half of the graphic window, the indicator of the second slider will follow the mouse.
Then according to the position of the mouse the `servoWrite` function writes a value to the servo telling to go to the corresponding angle ranging from 0 to 180 degrees.

The code is as follows:

```js
...
if (mousePressed && mouseY < y1+20) {
      float targetX1 = constrain(mouseX, 100, 380);
      float dx = targetX1 - x2;
      x2 += dx * easing;
      arduino.servoWrite(5, constrain(mouseX / 2, 0, 180));
  }
 if (mousePressed && mouseY > y4-10) {
      float targetX2 = constrain(mouseX, 100, 380);
      float dx = targetX2 - x4;
      x4 += dx * easing;
      arduino.servoWrite(9, constrain(mouseX / 2, 0, 180));
  }
  ```
 
 Below the graphic window with the created sliders:
  
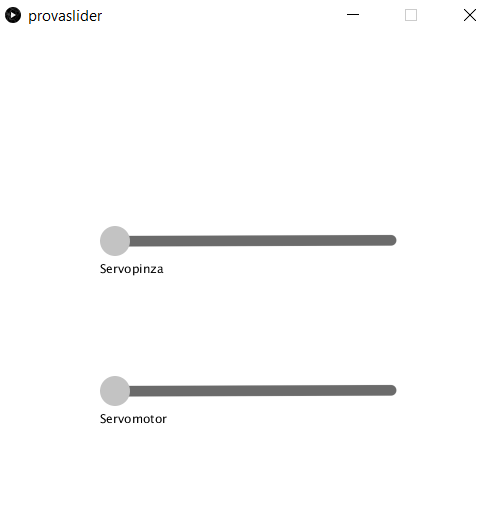
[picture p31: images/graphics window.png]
slider
  
  
#### Graphic

In order to view the data coming from the EMG we have created a graph on Processing in which we can see the trend recorded by the EMG.
To improve the code we have created multiple classes, so that the main sketch is more compact. For the graph we have `public class Grafico`.
to build the graph the axes were drawn first, by using the function `line(x1, y1, x2, y2)`, the values contained inside indicate the position in which the graph has been placed and also the length of the x and y axes which represents respectively the time t(s) and the amplitude V of the oscillations of the EMG.

Inside `public void setdat()` we define an array of 1000 elements and through a for cycle we have access to the element of the array which are the values from the EMG remapped between 0 and 300 (which corresponds to the height of the y axis). Then we define another array which contans as much element as the previous one, again we access to the elements through a for cycle and we define a float variable called `passo` which is the length of the x axis divided by the float variable `data.lenght`. So the value assumed by the elements of the `datax[i]` array is 50 + i * passo.
the code is as follows:

```js
public class Grafico {
public float[] datax; 
 public Grafico(){}
 
 public void setdati(){
 data = new float[1000];
  for (int i=0; i < data.length; i++) {
    data[i] = 100;
  }
  datax = new float[data.length];
  for (int i=0; i < datax.length; i++) {
    float passo=900/float(data.length);
    datax[i] = 50+i*passo;
  }
 }
```  
So once we have defined the relationship between the data received and the x axis we can draw the line which allows us to view the trend of the values detected by the EMG with `line(datax[i], 650-data[i], datax[i+1], 650-data[i+1])`. Once the curve reaches the end of the x axis restart from the origin. 
The direction of the axes indicated by the tip of an arrow and have been created with the triangle function in which the six values represents the position of the three vertices of the triangle.

```js
public void assi(){
 for (int i=0; i<data.length-1; i++) {
    fill(55, 200, 50);
    line(datax[i], 650-data[i], datax[i+1], 650-data[i+1]);
  }

  stroke(0, 0, 250);
  strokeWeight(2);
  //line(50,800-V,950,800-V);
  stroke(0, 0, 0);
  line(50, 350, 50, 650);
  line(50, 650, 950, 650);
  fill(0, 0, 0);
  triangle(48, 350, 52, 350, 50, 340);
  triangle(940, 648, 940, 652, 950, 650);
  textSize(12);
  text("t(s)", 965, 665);
  text("V(v)", 15, 350);
 }
``` 
#### Icon

The icon was added in order to switch the command so that it is possible to control the clamp with the sliders. The switch allows us to switch to manual control. In order to create the switch we have used the Cp5 library which contains the switch among the examples.
it was therefore necessary to import the library:

```js
import controlP5.*;
ControlP5 cp5;
``` 
In the `public class Serialcomunication extends Grafico` we created a function `serialsend()` in which if the manual control is active (`if (pulsante == true)`) and if the mouse is pressed and it is in correspondence with one of the sliders, we can open-close the gripper or rotate it by mapping the position on the slider in the range between 0° and 180° for the gripper and between -90° and 90° for the rotation. Then this value is written as String together with an identification character to the serial port.
the code is as follows:

```js
...

 void serialsend() {
    if (mousePressed) {
      if (millis()-ti>500) {
        if (pulsante==true) {
          if (mousePressed && mouseY < y2+20) {
            float pinzamap=map(target1, 50, 350, 0, 180);
            String pinza="P"+str(pinzamap);
            MyPort.write(pinza);
            println(pinza);
          }
        }

        ti=millis();
      }
      if (millis()-ti2>500) {
        if (pulsante==true) {
          if (mousePressed && mouseY > y4-20) {
            float rotazmap=map(target2, 50, 350, -90, 90);
            String rotaz="R"+ str(rotazmap);
            MyPort.write(rotaz);
            println(rotaz);
          }
        }
        ti2=millis();
      }
    }
  }
  ...
  
``` 
If we click on the icon which has the value “false” by default we give the value `true` and the string `"C1"` is sent on the serial, otherwise if the value is `false` the string `"C0"` is sent on the serial. When the string `"C1"` is read from the serial the boolean variable `controlloapp` is seto to 1 so that the movements of the gripper will be managed by the sliders. 
Instead if the string `"C0"` is read from the serial the Boolean variable `controlloapp` is set to 0 so that that the movements of the gripper will be managed by values received from the inertial sensor and the emg sensor which means that the manual control is disabled.
```js
void icon(boolean theValue) {

  println("got an event for icon", theValue);
  if (theValue == true) {
    MyPort.write("C1");
    pulsante=true;
  }  
  if (theValue == false) {
    MyPort.write("C0");
    pulsante=false;
  }
} 
``` 
We have created virtual displays to read the values coming from the sensors. In particular one for the beat, one for the inclination of the gripper, one for the temperature and for the temperature we also drew a thermometer.
Let’s start with the beat.

#### Bpm

To view the beat we imported the image of a heart inside which the value is written. As for the images used for the sliders we first loaded the image, previously saved in the program folder, and than we pasted it with the `image()` function.
The continuously updated value of the beat derives from the `text()` function in which as string we have inserted `nfn(Batt, 0)` which transforms the float variable `Batt` containing the values of the beats transmitted via bleutooth by the Arduino Uno into a String, with 0 digit to the right of the decimal point.
```js
public void cuore(){
        battitook = loadImage("battitook.png");

  }

...
public void battito (float Batt){
  textFont(font24); 
  fill(250, 0, 0); 
  text("BPM", x1+xshift+950, y1-10); 
  fill(0, 0, 0);
  image(battitook, x1+900, y1+20);
  text(nfc(Batt, 0), 1017, 150);
  }

```

#### Roll

In the icon called Roll we have reported the values of the inclination of the gripper. We simply created a rectangle with the `rect()` function inside which we entered the value in the same way as for the beat, this time using the float variable `float Incl`.
```js
public void inclinazione(float Incl) {
    fill(190);
    stroke(0);
    strokeWeight(1);
    rect(700, 70, 180, 140, 7);
    fill(0, 0, 0);
    textFont(font24);
    text("Roll", 760, 40);
    text(" °", 800, 150);
    text(nfc(Incl, 1), 770, 150);
  }

```
Exactly the same thing was done for the rectangle in which the temperature value is reported, obviously with the appropriate variable and for this we omit the corresponding code.

#### Thermometer

In order to create the thermometer the bulb was drawn first with the function `ellipse()` which draws an ellipse with center X,Y and semi-axis equal to width and height. The bulb is filled with mercury so it has been colored with shade of red.
Then you have to draw the thermometer which is given by the union of an arc and a rectangle so we have used the functions `arc()` and `rect()`. The function  `arc()` contains different values, in order we have the X and Y position of the center, the width and the height but also the start angle and the end angle. 
Once the bulb and the thermometer are built the inside of the thermometer is filled with mercury. In order to build the mercury column that signals the detected temperature it has been use the function `map(tempC, 0, 50, 0, 175)` which maps che temperature between 0 and 50 degrees in the height of the graduated scale. 
`h = -y-66` is the offset between the zero and the bulb. 

The code is as follows:

```js
public class Termom {
  float y, h;
  
  public Termom() {
  }
  //Disegno termometro
  public void bulbo() {
    // Bulbo
    fill(200, 0, 0);
    smooth();
    stroke(0, 46, 200);
    strokeWeight(8);
    ellipse(1250, 550, 58, 50);
  }

  public void termometro() {
    //Termometro
    noStroke();
    fill(0, 46, 200);
    arc(1250, 330, 30, 20, PI, PI+PI);
    rect(1235.2, 330, 30, 200);
  }

  public void mercurio() {
    // Disegno solco mercurio
    fill(250, 250, 250);
    rect(1245, 330, 10, 200);
    
    // Mercurio
    fill(200, 0, 0);
    smooth();
    strokeWeight(0);
    float y= map(tempC, 0, 50, 0, 175); 
    h = -y-66; 
    rect(1245.2, 570, 10, h);
  }
```
The centigrade scale was also added. In particular a large notch has been added every ten degrees and a smaller one halfaway between the two large notches. 
The notches have been drawn with the `line()` command. 

#### Bluetooth decode 

Bluetooth performs two important functions.
The first one involves the manual control switch. 

When the switch is activated a command coded `Cx` is sent. `x` represents the state of the system. If it is `1` then the control will be manual otherwise it will be left to the sensors.

In addition to sending this command, the angular values for the servomotors are sent which will be received, decoded and implemented by the functions `pos_servo2(angle)`and `pinzacontrol2(angle)` in the servo motors structure. 
To send these commands there is a double check by checking the mouse pressed on the slider coordinates and by a non-blocking timer to avoid errors in the receiving serial buffer.

```js
if (millis()-ti>500) {
        if (pulsante==true) {
          if (mousePressed && mouseY < y2+20) {
            float pinzamap=map(target1, 50, 350, 0, 180);
            String pinza="P"+str(pinzamap);
            MyPort.write(pinza);
            println(pinza);
          }
        }

        ti=millis();
      }
```
Rotation is remapped and coded with `P` for the gripper and `R` for angular rotation.

The other important function is to receive temperature, rotation and electromyography data

To do this `serialreceive()` function was implemented.

```js
 if (MyPort.available() > 0) {
      dati = MyPort.readStringUntil('\n');
      dati=dati.trim();
    }
    dativec=dati.charAt(0);
    if (dativec == 'T') {
      valore = "";
      for (int i = 1; i < dati.length(); i++) {
        valore = valore +dati.charAt(i) ;
      }
      tempC = float(valore);
    }
// ecc.
```

This function checks for input data and converts it to a `char array`. Then check the first element to decode the data, convert the value to a number (`float` or `int`) and update the variable.

#### Code 

To make the code more readable and functional, various classes have been created containing the various graphic and functional elements.
There are different classics for:

- Thermometer 
- Virtual screens for data visualization
- Slider
- Serial and bluetooth comunication
- Switch controll 
- EMG chart

The various classes are linked in order to pass the most important variables to each other.

Within each class various objects have been created to implement the various functions. 
It is very interesting, for example, how these three different objects are called up in the data visualization class:

```js
  schermo.temperaturadigitale(tempC);
  schermo.inclinazione(Incl);
  schermo.battito(Batt);
```

To draw and update the three virtual displays.

This allowed us to obtain a much more opulent and organized final code. The code is as follows:

```js
import controlP5.*;
ControlP5 cp5;
import processing.serial.*;
Serial MyPort;
float target1;
float target2;
PFont font24;
PFont font12;
boolean pulsante=false;
float tempC = 0;
float Incl = 0;
float Batt=0;

Termom termom= new Termom(); 
Schermo schermo=new Schermo();
Slider slider=new Slider();
Serialcomunication serialcomunication=new Serialcomunication();
Switchcommand switchcommand = new Switchcommand();
Grafico grafico = new Grafico();

void setup()
{
  size(1400, 700);
  background(255);
  MyPort =  new Serial(this, "/dev/tty.HC-05-SerialPort", 9600);
  grafico.setdati();
  cp5 = new ControlP5(this);
  switchcommand.setup();
  schermo.cuore(); 
  slider.sliderset();
}

void draw()
{
  background(255);
  serialcomunication.serialreceive();
  grafico.assi();
  termom.disegna();
  slider.slider1();
  slider.slider2();
  schermo.temperaturadigitale(tempC);
  schermo.inclinazione(Incl);
  schermo.battito(Batt);
  serialcomunication.serialsend();
}

void icon(boolean theValue) {
  println("got an event for icon", theValue);
  if (theValue == true) {
    MyPort.write("C1");
    pulsante=true;
  }  
  if (theValue == false) {
    MyPort.write("C0");
    pulsante=false;
  }
} 
```
### Python app 

Another possibility is to use Python to develop the application. Python is a more "high level" programming language than most other languages, object oriented, suitable for working quickly and integrating different systems.

python

The [Pyserial](https://pyserial.readthedocs.io/en/latest/#) library for serial communication comes in handy.

To easily develop the graphical interface we relied on [Tkinter Designer](https://github.com/ParthJadhav/Tkinter-Designer) which allows us to convert a design made with [Figma](https://www.figma.com) with drag and drop into a python snippet. 
We started by simply devising the main window design:

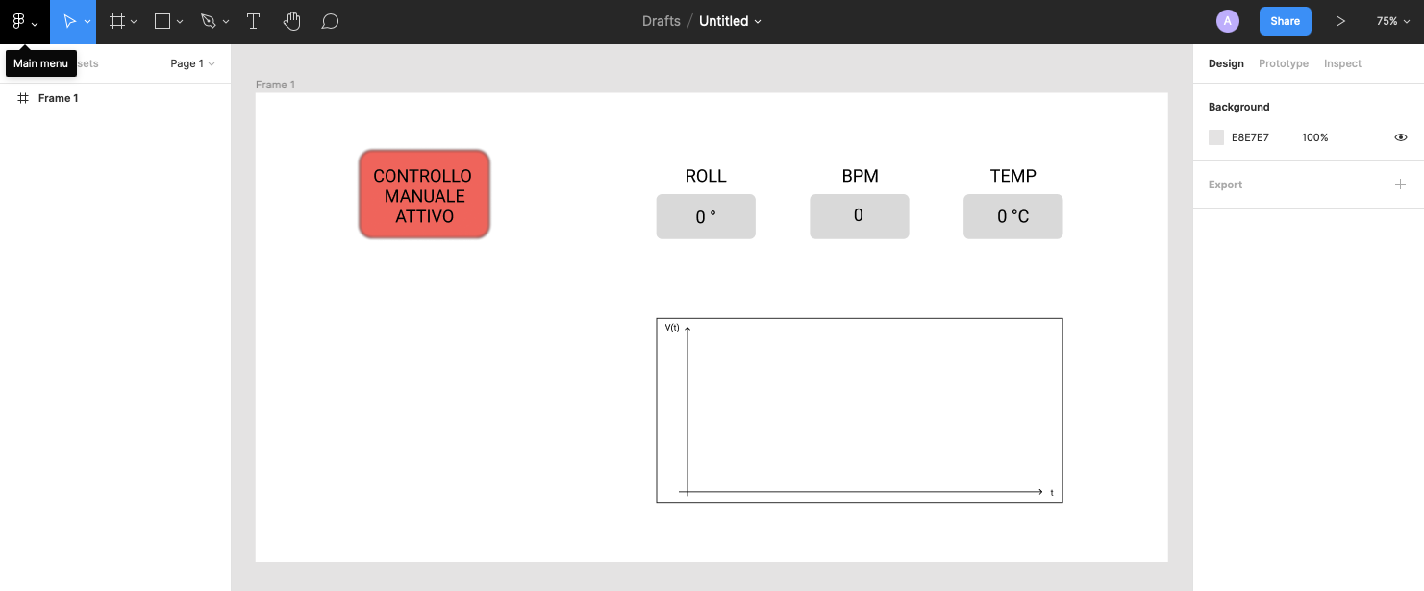
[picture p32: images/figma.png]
Figma


Then we modified the various blocks manually by introducing the labels and the whole part.

To insert the sliders we have created a Frame in which we have inserted the two sliders. We have inserted all of them with the `.pack ()` method:

```py
win = Frame(window)
win.pack(side =LEFT,fill=None, expand=False)
spinza = Scale(win, from_=0, to=180,orient=HORIZONTAL,command=spinza_changed)
spinza.pack(side=BOTTOM, padx=120, ipadx=60)
spinza.set(90)
sroll = Scale(win, from_=0, to=180,orient=HORIZONTAL,command=sroll_changed)
sroll.pack(side=BOTTOM, pady=100,  ipadx=60)
sroll.set(90)
```

And to send data:
```py
def spinza_changed(event):  #viene attivata quando varia lo slider spinza
    time.sleep(0.3) #aspettano 100 ms per evitare di stampare tutti i valori dello slider che si muove
    print("P"+str(spinza.get())) #stampa codificata
    if (bottone==False): #solo se sono in controllo manuale
        #invio i dati sulla seriale convertendoli in un byte (aggiungo anche i fine riga)
        #sfrutto la codifica concatenando P, il valore degli slider e i fine riga
        #byte con codifica utf-8
        arduino.write(bytes("P"+str(spinza.get())+"\r\n", 'utf-8'))
    
def sroll_changed(event):  #viene attivata quando varia lo slider sroll
    time.sleep(0.3) #aspettano 100 ms per evitare di stampare tutti i valori dello slider che si muove
    print("R"+str(sroll.get())) #stampa codificata
    if (bottone==False): #solo se sono in controllo manuale
        arduino.write(bytes("R"+str(sroll.get())+"\r\n", 'utf-8')) #invio i dati sulla seriale (vedi fz precedente)
```

The control button is actually fake as it consists of two images that are interchanged:
```py
img0 = PhotoImage(file = f"img0.png")
img1 = PhotoImage(file = f"img1.png")
b0 = Button(
    image = img0,
    borderwidth = 0,
    highlightthickness = 0,
    command = btn_clicked,
    relief = "flat")
b0.place(
    x = 143, y = 79,
    width = 180,
    height = 123)
```

```py
def btn_clicked(): #fz per aggiornare il pulsante, viene richiamata quando cliccato
    global bottone #utilizzare variabili globali
    # print("Button Clicked") 
    if (bottone): #siamo in controllo automatico5
        b0.config(image = img1) #aggiorna l'imm in rosso
        print("C1") #per cambiare modalità su arduino
        arduino.write(b'C1\r\n') #invio i dati sulla seriale convertendoli in un byte (aggiungo anche i fine riga)
    elif (bottone==False): #se siamo in controllo manuale
        b0.config(image = img0) #aggiorna l'imm in grigio
        print("C0") #per cambiare modalità su arduino
        arduino.write(b'C0\r\n') #invio i dati sulla seriale convertendoli in un byte (aggiungo anche i fine riga)
        #reset degli slider
        spinza.set(90)
        sroll.set(0)
    bottone=not(bottone) #cambia lo stato quando viene premuto il pulsante
    # print(bottone)
```

To receive data continuously, an `arduinoreceive()` function has been added, called by an `.after` method within a label that is continuously updated. This function is called at the end of the code for the first time. 
We start by initializing the serial:

```py
import serial
arduino = serial.Serial(porta, 9600)
```
The function reads the variables of the graph (which we will talk about later) and the position indices. Starts by deleting the graph to update it and goes to read the text on the serial `.readLine()`.
It converts the received text as a byte and checks the first letter to decode the value. It then updates the labels `.itemconfigure(label_name,text=testo.replace('T', '')+" ° C")` or values for the chart. Inserting the values the replace function deletes the encoding letter.
To update the graph values, the index is increased every lap. Then it is drawn.

```py
def arduinoreceive(): #funzione per ricevere
    #importo i grafici per poterci lavorare
    global a
    global b
    #resetto il grafico cancellandolo
    canvas.delete(a)
    canvas.delete(b)
    #importo gli indici per poterci lavorare
    global indicem
    global indices
    testo= arduino.readline() #legge la riga
    testo=testo.rstrip() #elimina i caratter '\r\n'
    testo=testo.decode("utf-8")  #utilizza la codifica corretta
    #print(testo)
    canvas.itemconfigure(grafico,fill='white') #aggiorno lo sfondo del grafico
    canvas.itemconfigure(text,text=str(testo)) #aggiorna l'etichetta per il debug
    window.after(50, arduinoreceive) #quando cambiano le etichette richiama la funzione creando un loop
    #iniziamo la decodifica
    if testo[0]=="T":
     #   print("Temperatura = "+testo.replace('T', ''))
        canvas.itemconfigure(temp_label,text=testo.replace('T', '')+" ° C")
    if testo[0]=="A":
     #   print("Angolo = "+testo.replace('A', ''))
        canvas.itemconfigure(roll_label,text=testo.replace('A', '')+" °")
    if testo[0]=="B":
     #   print("Bpm = "+testo.replace('B', ''))
        canvas.itemconfigure(bpm_label,text=testo.replace('B', ''))
    if testo[0]=="M":
        #vado ad aggiornare il valore corrispondnete all'ordinata del grafico
        #utilizzo la funzione mappa per mappare nell'intervallo corretto passandogli il testo senza il primo carattere
        data_m[indicem]=mappa(testo.replace('M', ''))
     #   print(f"data_m{indicem}]="+str(data_m[indicem]))
      #  print(indicem)
        indicem+=1 #incremento l'indice
    if testo[0]=="S":
        data_s[indices]=mappa(testo.replace('S', ''))
        indices+=1
        #disegno il grafico della media (average) unendo le coordinate di tutti i punti
    a=canvas.create_line( 'SEE LATER' )
    #disegno il grafico della soglia unendo le coordinate di tutti i punti
    #questo grafico NON viene attualmente utilizzato in quanto non vengono aggiornati i valori
    b=canvas.create_line( 'SEE LATER' )
    #se necessario resetto l'incremento dell'indice
    if indicem==rangemax:
        indicem=0
    if indices==rangemax:
        indices=0
```

The graph is constructed by joining 200 points whose coordinates are contained in the `datax` and `data_m` lists. These lists were created separately with the `vector.py` and `datilinea.py` scripts.

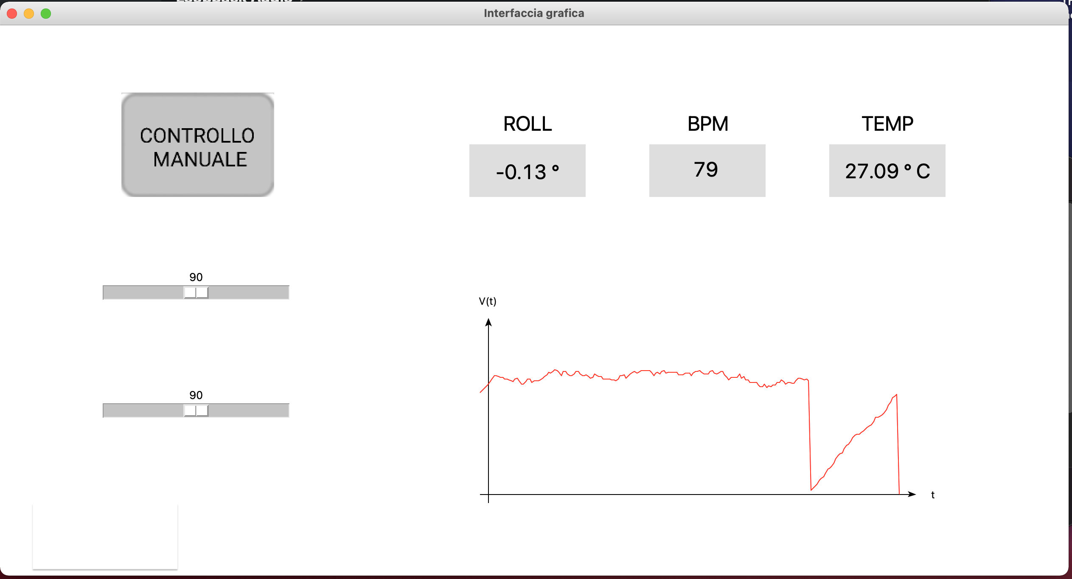
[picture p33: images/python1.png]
Python


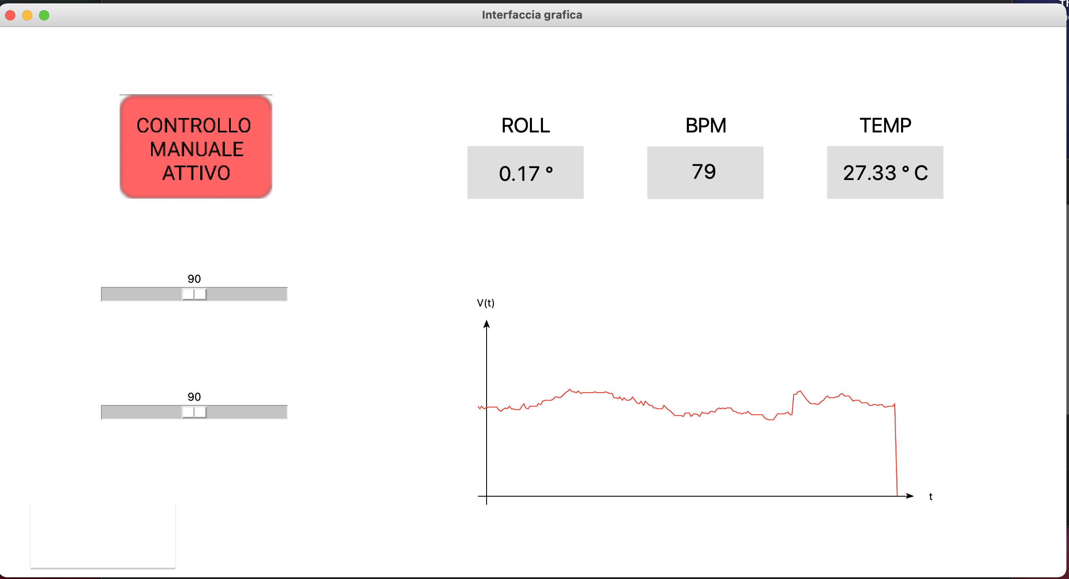
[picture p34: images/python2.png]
Python


The sliders were created with the `Scale()` command and placed with `pack()`.

```py
spinza = Scale(win, from_=0, to=180,orient=HORIZONTAL,command=spinza_changed) #creiamo il widget con Scale
spinza.pack(side=BOTTOM,padx=120,  ipadx=60) #allineiamo lo slider e lo allarghiamo
spinza.set(90) #mettiamo l'indicatore al centro
slider1_label = ttk.Label(win,text=" CONTROLLO PINZA ",relief='groove',padding='3')
slider1_label.pack(side=BOTTOM)
#creiamo il secondo slider
sroll = Scale(win, from_=-90, to=90,orient=HORIZONTAL,command=sroll_changed)
sroll.pack(side=BOTTOM,  ipadx=60)
sroll.set(0)
slider_label = ttk.Label(win,text=" CONTROLLO ROTAZIONE ",relief='groove',padding='3')
slider_label.pack(side=BOTTOM)
```

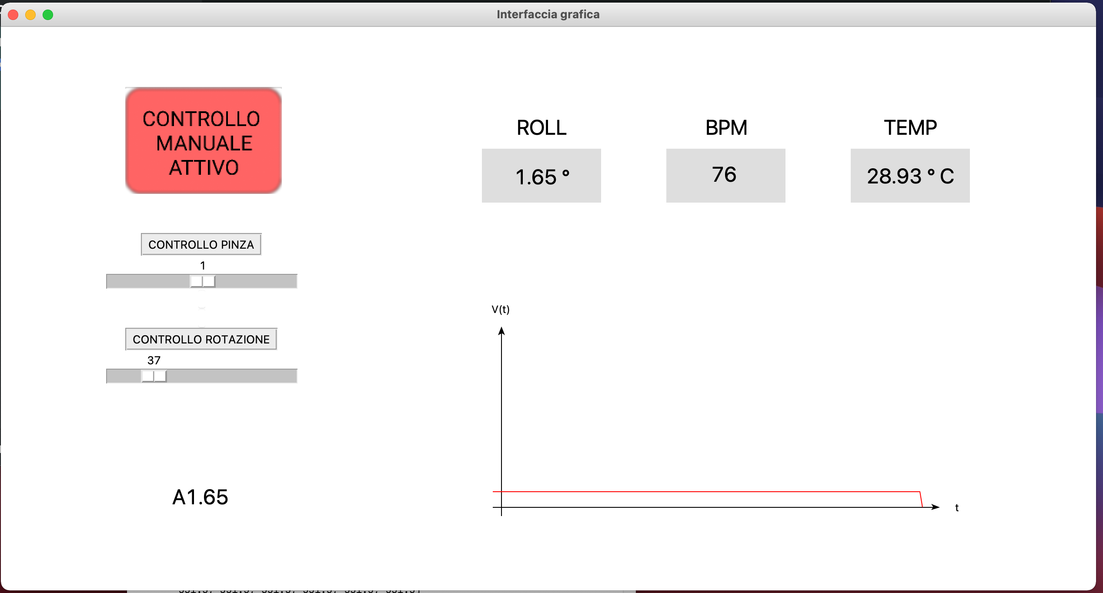
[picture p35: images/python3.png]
Python


### Mobile app

To create application for smartphone has been used [MIT App Inventor](https://appinventor.mit.edu). App inventor allows us to develop a complete and functional app with an easy process however this application works only on Android devices. 

The functionalities are the same as those of the computer app integrated with portability and ubiquity of smartphone.  

To develop application the first thing to do is to add all the necessary components like list picker, label, slider, bluetooth client, clock and buttons. 

The Blocks have been created separately step by step. As follows is the result of the various tests performed. The graphic has been ultimated at the last. 

First of all it is necessary to create the structure that allows to select the bluetooth mac address of bluetooth module (HC-05).

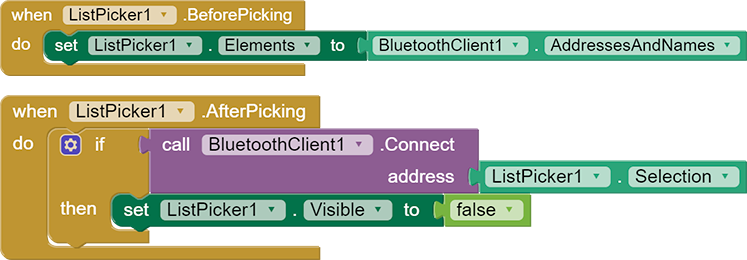
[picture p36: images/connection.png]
connection


Then in order to change from automatic to manual control has been created a switch like block that send `C0`or `C1`with the same coding rules of processing app. 

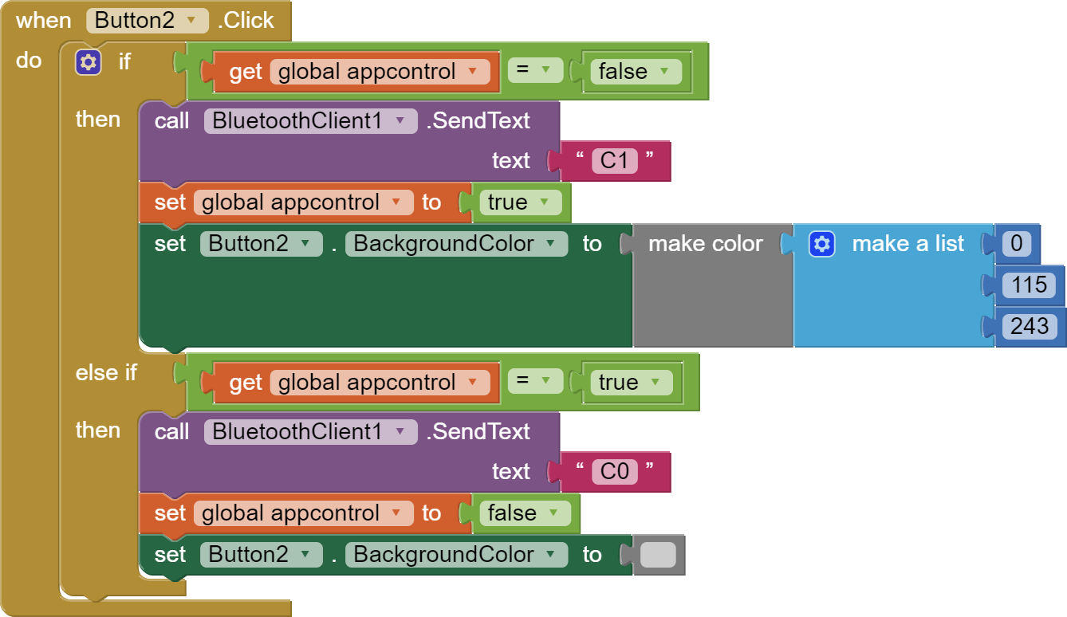
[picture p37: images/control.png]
control


When manual control is on (`appcontrol == true`) it is possibile to send data. For example has been used the gyroscope of the smartphone to simulate the rotation of the clamp. 

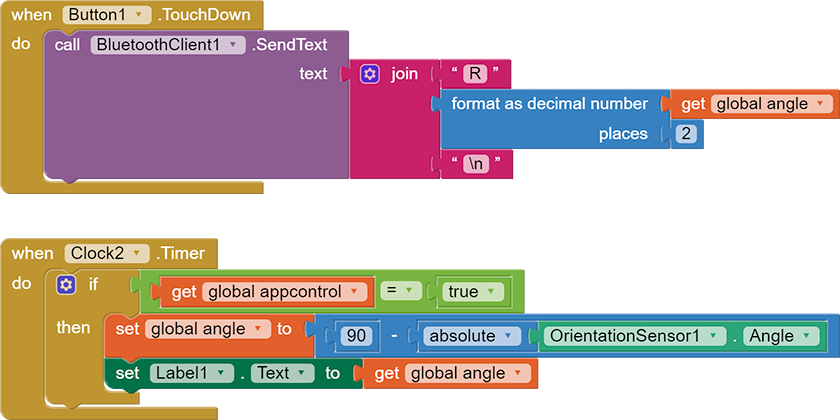
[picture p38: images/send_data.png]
send_data


To receive data it is necessary to request the availability of pipe and to save data in new variables.

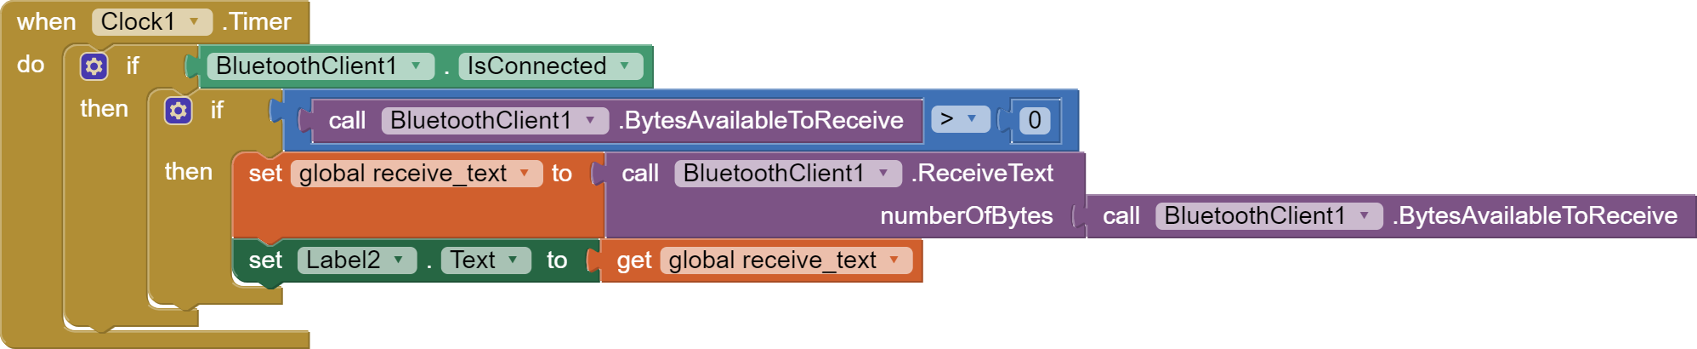
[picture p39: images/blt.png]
blt


According to the type of the variables provided by App Inventor it has been necessary to split the string containing the received data into a `list`. This list `decode_text` contains different elements each of which represents a new codified upgraded data. Then each element has been analized by control the first character and saving the corrisponding value into the relative variable. 

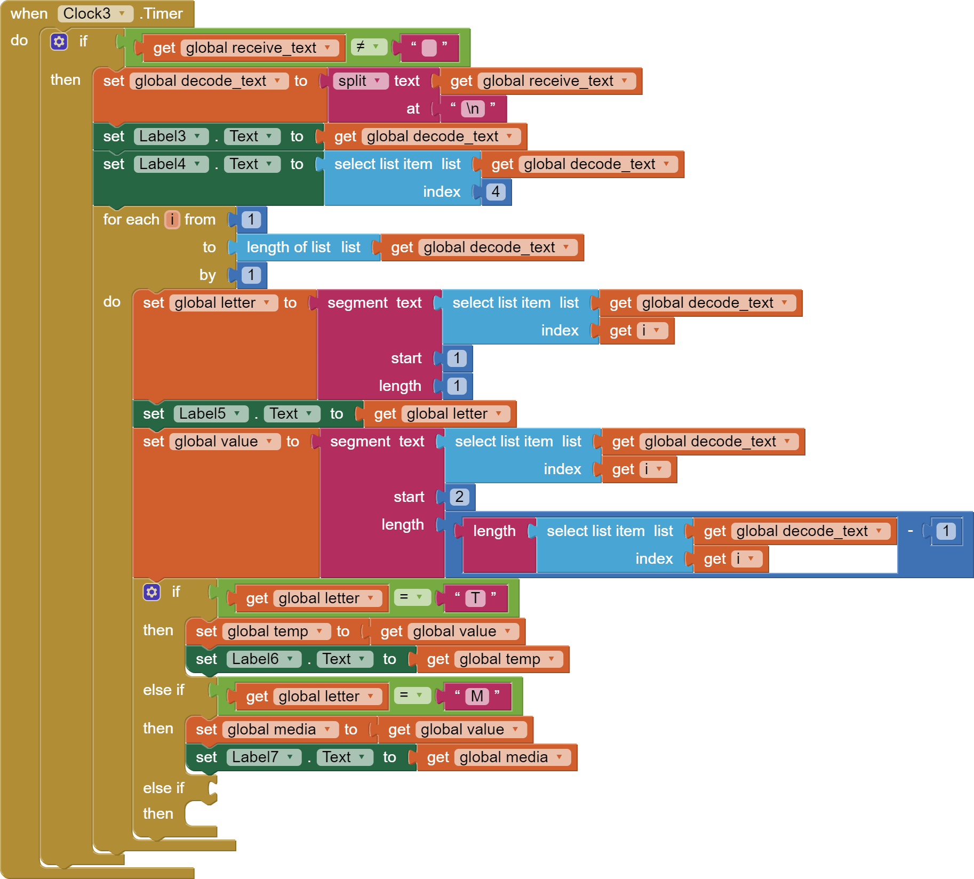
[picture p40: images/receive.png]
receive


At this point has been used a test graphic interface to check that all works. 

mobile1

Graphic layout has been ultimated.

The final block structure:

mobile1

Final app layout:

mobile1

___

### iOS App 

To develop the application for devices with iOS mobile system it is first necessary to replace the bluetooth protocol with the BLE protocol. The Bluetooth Low Energy is independent of classic Bluetooth and has no compatibility, but they can coexists. BLE is intended to provide considerably reduced power consumption and cost while maintaining a similar communication range.
All Bluetooth Low Energy devices use the Generic Attribute Profile (GATT). The application programming interface offered by a Bluetooth Low Energy aware operating system will typically be based around GATT concepts. GATT has the following terminology:
- Client, a device that initiates GATT commands and requests, and accepts responses, for example, a computer or smartphone.
- Server, a device that receives GATT commands and requests, and returns responses, for example, a temperature sensor.
- Characteristic, a data value transferred between client and server, for example, the current battery voltage.
- Service, a collection of related characteristics, which operate together to perform a particular function. For instance, the Health Thermometer service includes characteristics for a temperature measurement value, and a time interval between measurements.
- Descriptor, provides additional information about a characteristic. 

GATT

Services, characteristics, and descriptors are collectively referred to as attributes, and identified by UUIDs. A universally unique identifier (UUID) is a 128-bit (16 bytes) number that is guaranteed (or has a high probability) to be globally unique. For efficiency, and because 16 bytes would take a large chunk of the 27-byte data payload length of the Link Layer, the BLE specification adds two additional UUID formats: 16-bit and 32-bit UUIDs. These shortened formats can be used only with UUIDs that are defined in the Bluetooth specification (i.e., that are listed by the Bluetooth SIG as standard Bluetooth UUIDs).

To reconstruct the full 128-bit UUID from the shortened version, insert the 16- or 32-bit short value (indicated by xxxxxxxx, including leading zeros) into the Bluetooth Base UUID: `xxxxxxxx-0000-1000-8000-00805F9B34FB`.

___

A DSDTech SH-HC-08 module was used. The connection with Arduino remains the same as the HC-05 module using the default serial port on pins 0-1. 
On the iOS device the LightBlue application was used to read the module information such as Characteristic UUID.

UUID

The DSD TECH Bluetooth application was also used to test the device for both reading and writing:

DSDAPP

So we moved on [Thunkable](https://thunkable.com/#/) to develop the app. Thunkable allows us to develop an app in the same way as MIT App Invetor but also compatible with iOS. 

The graphical interface was designed in a similar way to what was done for android with App Inventor. The differences lie in the bluetooth communication. 

After several problems we have prepared a simplified interface with different labels and buttons to test the functionality. When the `Scan` button is clicked, the devices are scanned and shown in the first label. Then with the `Connect` button you connect to the default device (without the possibility of choosing others) and finally there is the possibility to send / receive data each time the `Send` button is pressed.

Thunkable

So we tested the app.

> At this point there is an issue with the app **which appears to be due to the thunkable's BLE interface**. Doing several tests on Android it turns out an `undefined` error during scanning. On iOS, on the other hand, the scanning and connection are perfectly successful but it is not possible to send / receive the data, which works with other apps with a serious interface. 

We are awaiting answers on Thunkable support. Searching the forum for references to problems in the BLE blocks.

## Data logging and storage

Given the recent interest in telemedicine it seemed appropriate to allow the storage of the experiment data directly in a remote server, giving the possibility to view them remotely and after. 

An environmental temperature and humidity sensor has also been integrated. 

Data are saved on a MySQL database reachable from a domain owned by one of us authors. 

For the visualization of the data we relied on the [Highcharts](https://www.highcharts.com/blog/products/highcharts/) libraries, a software library for dynamic charting written in pure JavaScript.

### Esp 8266

We have added a second device in order to make the system completely modular allowing you to add this step to save data remotely if you wish.
The NodeMCU is an open source platform developed specifically for the IOT, It includes a firmware that works through the ESP8266 SoC Wi-Fi module and hardware with the ESP-12E module base. To communicate with the computer it uses a CH340 chip.

The board is very powerful and we could have used it directly instead of arduino nano however we wanted to leave the modular system with the possibility of adding or not this functionality.

esp8266

To read the data from Arduino Nano we have implemented a serial software on pin 3 and 4 transmitting the data with the same coding logic used in the previous steps.
From the side of the Arduino nano:

```c
void trasmitt (String param, String val) {
    invio = param + String(val);
    mySeriale.println(invio);
}
```

By passing it the different parameters such as `trasmitt("T", String(tempmpu))`.

On the ESP side we initially cleaned the string of extreme formatting characters (`decodeserial()`) and then passed it to a second function that takes care of transforming it into an char array (`process()`) and finally the actual decoding by updating the variables (`analizestring()`).

Moreover the device was powered by the 5V of the Arduino Nano in order to switch them on together. 

We also implemented software serial on the nodeMCU with a dedicate library.
```c
#include <SoftwareSerial.h>
SoftwareSerial Esp_serial(D3, D4);
```

esp8266

### DHT 11 

An ambient humidity and temperature sensor has been added. A DHT11 read using the Adafruit library for DHT sensors.

We have implemented this in a dedicated library:

```c
#include "DHT.h"
#define DHTTYPE DHT11   // DHT 11
const int DHTPin = D5;
DHT dht(DHTPin, DHTTYPE);
float h;
float t;
unsigned long timea=0;

void letturadht() {
   if (millis() - timea > 500) {
    h = dht.readHumidity();
    t = dht.readTemperature();
    Serial.println(h);
    Serial.println(t);
  timea=millis();
   }
}
```

### MySQL Database

On the server side we have created a dedicated database with a custom user. We will need this data (`db_name` and `username`) to implement the code after.

Using phpMyAdmin we have created a table ready to accept all the variables of interest:

```sql
CREATE TABLE Sensor (
    id INT(6) UNSIGNED AUTO_INCREMENT PRIMARY KEY,
    tempmpu VARCHAR(10),
    angle VARCHAR(10),
    average VARCHAR(10),
    bpm VARCHAR(10),
    soglia VARCHAR(10),
    temp VARCHAR(10),
    hum VARCHAR(10),
    reading_time TIMESTAMP DEFAULT CURRENT_TIMESTAMP ON UPDATE CURRENT_TIMESTAMP
)
```

### POST Request

To send data we use HTTP POST request. By design, the POST request method requests that a web server accepts the data enclosed in the body of the request message, most likely for storing it.

We must therefore connect the esp 8266 to the internet through the wifi library. You must also include a library for HTTP.

A function has been implemented that repeatedly sends a text message containing the variables concatenated in a string that the server will decode and position the data correctly.

```c
#include <ESP8266WiFi.h>
#include <ESP8266HTTPClient.h>
//timer
unsigned long t2 = 0;
unsigned long dt = 0;
unsigned long t3 = 200;//update database every

void servercall () {
  if (WiFi.status() == WL_CONNECTED) {
    HTTPClient http;
    http.begin(serverName);    
    http.addHeader("Content-Type", "application/x-www-form-urlencoded");
    dt = millis() - t2;
    if (dt >= t3) {
      String httpRequestData = "api_key=" + apiKeyValue + "&tempmpu=" + String(tempmpu)
                               + "&angle=" + String(angle) + "&average=" + String(average) 
                               +  "&bpm=" + String(BPM) + "&soglia=" + String(soglia)
                               + "&temp=" + String(t) + "&hum=" + String(h) + "";
      int httpResponseCode = http.POST(httpRequestData);
      t2 = millis();
    }
    http.end();
  }
}
```

Sensitive data such as wifi passwords and database usernames are saved in the `sensdata.h` file.

So the main code is as follows:

```c
#include "serialreceive.h"
#include "dhtread.h"
#include "wifidata.h"
void setup() {
  Serial.begin(9600); 
  Esp_serial.begin(9600); 
  dht.begin();
  WiFi.begin(ssid, password);
  Serial.println("Connecting to WiFi");
  while (WiFi.status() != WL_CONNECTED) {
    delay(1000);
    Serial.println(".");
  }
  Serial.println(WiFi.localIP());
}
void loop() {
  letturadht();
  servercall();
  decodeserial();
  delay(1);
}
```

A php page is called up on the server and takes care of decoding the data. 
The function takes care of receiving the complete string and identifying the various concatenated variables in the prescribed order, then absorbing them in the reference column by inserting it in the table. It also marks the time of insertion.

```php
<?php

$servername = "localhost";
$dbname = "dbname";
$username = "username";
$password = "user_pw";
$api_key_value = "APIKEY";
$api_key = $tempmpu = $angle = $average = $bpm = $soglia = $temp = $hum = "";
if ($_SERVER["REQUEST_METHOD"] == "POST") {
    $api_key = test_input($_POST["api_key"]);
    if($api_key == $api_key_value) {
        $tempmpu = test_input($_POST["tempmpu"]);
        $angle = test_input($_POST["angle"]);
        $average = test_input($_POST["average"]);
        $bpm = test_input($_POST["bpm"]);
        $soglia = test_input($_POST["soglia"]);
        $temp = test_input($_POST["temp"]);
        $hum = test_input($_POST["hum"]);
        $conn = new mysqli($servername, $username, $password, $dbname);
        if ($conn->connect_error) {
            die("Connection failed: " . $conn->connect_error);
        } 
        $sql = "INSERT INTO Sensor (tempmpu, angle, average, bpm, soglia, temp, hum)
        VALUES ('" . $tempmpu . "', '" . $angle . "', '" . $average . "',
                '" . $bpm . "','" . $soglia . "','" . $temp . "','" . $hum . "')";
        if ($conn->query($sql) === TRUE) {
            echo "New record created successfully";
        } 
        else {
            echo "Error: " . $sql . "<br>" . $conn->error;
        }
        $conn->close();
    }
    else {
        echo "Wrong API Key provided.";
    }
}
else {
    echo "No data posted with HTTP POST.";
}
function test_input($data) {
    $data = trim($data);
    $data = stripslashes($data);
    $data = htmlspecialchars($data);
    return $data;
}
```

### Data visualizing 

To read the data another php page is called. The code is divided into three sections. The first takes care of taking data from the database, a second takes care of the HTLM structures and a third of the graphs with the Highchart libraries.

datachart

The web page with the data is accessible at the [following link](http://tempcontrol.it/progelettronica/chart.php?pwd=elettronica) or with this short link: [bit.ly/datiprogettoelettronica](http://bit.ly/datiprogettoelettronica). 

The web page is password protected with a php algorithm, insert `elettronica`.

A structure php page has been created in different sections. 

A first section deals with calling the database and reading the latest values. Yhis is also contained in the `call.php` file.
Then it saves the data in variables that will be recalled from the graphs. Obviously we are talking about arrays.

```php
$readings_time = array_column($sensor_data, 'reading_time');
$tempmpu = json_encode(array_reverse(array_column($sensor_data, 'tempmpu')), JSON_NUMERIC_CHECK);
$angle = json_encode(array_reverse(array_column($sensor_data, 'angle')), JSON_NUMERIC_CHECK);
$average = json_encode(array_reverse(array_column($sensor_data, 'average')), JSON_NUMERIC_CHECK);
$bpm = json_encode(array_reverse(array_column($sensor_data, 'bpm')), JSON_NUMERIC_CHECK);
$soglia = json_encode(array_reverse(array_column($sensor_data, 'soglia')), JSON_NUMERIC_CHECK);
$temp = json_encode(array_reverse(array_column($sensor_data, 'temp')), JSON_NUMERIC_CHECK);
$hum = json_encode(array_reverse(array_column($sensor_data, 'hum')), JSON_NUMERIC_CHECK);
$reading_time = json_encode(array_reverse($readings_time), JSON_NUMERIC_CHECK);
```

Then there is the html structure in which we have put different containers with their own style to organize the layout. 

```css
   body {
      min-width: 310px;
    	max-width: 90%;
    	height: 500px;
      margin: 0 auto;
    }
  .container { 
    position: center;
    column-count: 2;
    column-width: 50%;
    padding-top: 50px;
    }
```
And the page body:

```html
 <div class="container2">
    
    </div>

    <div class="containerinfo">

    </div>

    <div class="containerinfo">

    </div>

    <div class="containerinfo">

    </div>
```

By recalling the variables containing the data, the graphs are built using the highcharts libraries and therefore with a javascript snippet such as:

```js
// ---
var tempmpu = <?php echo $tempmpu; ?>;
// ...
var reading_time = <?php echo $reading_time; ?>;
// ---
var chartT = new Highcharts.Chart({
  chart:{ renderTo : 'chart-tempmpu', zoomType: 'x', panning: true, panKey: 'shift' },
  title: { text: 'Temperature' },
  series: [{ showInLegend: false, data: tempmpu }],
  plotOptions: {line: { animation: false, dataLabels: { enabled: false } }, series: { color: '#C80303' }},
  xAxis: { type: 'datetime', labels: { enabled: false }, categories: reading_time },
  yAxis: {title: { text: 'Temperature (Celsius)' } },
  credits: { enabled: false }
});
// ...
```

To this is added an additional algorithm to protect the display of the graphs with a password:

```php
$password = 'elettronica';
// -------------------------
$pwd = isset($_GET['pwd']) ? $_GET['pwd'] : false;
if (!$pwd || $pwd != $password) {
  ?>
<form method="get" action="<?php echo $_SERVER['PHPSELF']; ?>">
<table border="0" cellspacing="0" cellpadding="10">
<?php if ($pwd !== false): ?><tr class="errore"><td colspan="3">La password inserita non è corretta!</td></tr><?php endif; ?>
<tr>
  <td>Password</td>
  <td><input type="password" name="pwd" style="width: 180px;"/></td>
  <td><input type="submit" value="Entra"/></td>
</tr>
</table>
</form>  
  <?php  
}else{ 
  ?>
    // ALL THE CONTENTS
  <?php  
}
?>
```

The graphs are widely customizable in particular the possibility of zooming in a certain time interval and scrolling along the time axis has been activated. It is also possible to select a single value and read other information such as the save time

zoomchart

## Make it more compact

To make everything more compact and avoid the problems due to the lack of stability of the breadboards we decided to solder everything on a multi-hole circuit. However, to allow testing and component replacement we used multi-pin connectors. 

### Sensors cable

To allow easy transport and disassembly we have combined all sensors in a single cable.

The cable of the EMG with its 3.5 mm jack is excluded.
We used a Cat 5e cable with T568B Wiring scheme.

We connected together VCC and GND of the two sensors and the pulse sensor data arrives on pin A3.

The sensors were connected as follows:

sensorcable

### Reading station

In order to have a compact but at the same modular structure and that would allow to carry out different tests, we stacked several multi-hole prototype boards. 
There are also a 3.5mm female jack connector for the electromyography cable and an RJ45 connector for the sensor cable.
On the top floor there is the LCD display and the trimmer to adjust the threshold, easily accessible

readstation

### Power supply

To allow use without discharging the batteries or powering from a computer with usb we have recycled power supplies for electronic devices. 

powersupply

We used two different 9V power supplies by joining a clamp (+) with a (-) obtaining a ground reference in order to have +9V and -9V on the other two cables. This is to power the electromyography circuit

We added a 12V power supply to power the arduino nano from `Vin` which in turn powers the Esp8266 and the whole system.

We then connected everything in the base of the reading station so as to power everything with a single cable with C13 connector. 

Two switches have also been added in order to selectively access the system and the power supply for the EMG

basement

In conclusion, the entire data reading system looks like this:

finalstruc

## Conclusions and future developments

The temperature sensor does not report perfectly the temperature of the subject and could be replaced with a sensor in contact with the skin and possibly an algorithm designed to bring the peripheral temperature back to the central one.

The use of a more advanced EMG sensor such as MyoWare allows you to reduce noise and have a more compact structure.

To develop an application for iOS it is necessary to replace the bluetooth module with one with Bluetooth Low Energy such as the SH-HC-08 module. 

To increase data security with a view to respecting privacy and the GDPR regulations for the processing of personal data online, it is certainly necessary to provide a security algorithm that is much more serious than simply hiding the content of the page with the php script. In addition, it may be advisable to encrypt the data even before sending it to the server and to activate the HTTPS protocol on the web page.

For the environmental temperature and humidity it may be appropriate to replace the DHT11 with a DHT22, thus obtaining a sensitivity of 0.5 ° C and 2% RH.

For the power supply, instead of three power supplies, a single 18V power supply could be used with a voltage divider to obtain ± 9V.

Finally, the reading station could be redesigned on PCB in order to have a single more compact plane.

## References

- [nRF24L01 Wireless RF Module](https://components101.com/wireless/nrf24l01-pinout-features-datasheet)
- [Arduino Wireless Communication](https://www.youtube.com/watch?v=7rcVeFFHcFM)
- [EMG Circuit for a Microcontroller](http://www.instructables.com/member/Gundanium/?utm_source=pdf&utm_campaign=title)
- [Electromyography(EMG) with MyoWare Muscle Sensor & Arduino](https://how2electronics.com/electromyography-emg-with-myoware-muscle-sensor-arduino/)
- [Muscel Sensor V3 Datasheet](http://www.advancertechnologies.com/p/muscle-sensor-v3.html)
- [pulsesensor.com](https://pulsesensor.com)
- [FIAB elettrodi](https://www.fiab.it/prodotti.php)
- [LCD custom generator](https://maxpromer.github.io/LCD-Character-Creator/)
- [Fritzing standard](https://fritzing.org/learning/tutorials/creating-custom-parts)
- [Make your own fritzing parts](https://learn.sparkfun.com/tutorials/make-your-own-fritzing-parts/all)
- [Arduino smoothing](https://www.arduino.cc/en/Tutorial/BuiltInExamples/Smoothing)
- [Uno pinout guide](https://www.circuito.io/blog/arduino-uno-pinout/)
- [Nano pinout guide](https://www.makerguides.com/arduino-nano/)
- [ESP8266 pinout](https://randomnerdtutorials.com/esp8266-pinout-reference-gpios/)
- [Elettromiografia](https://it.wikipedia.org/wiki/Elettromiografia_ed_elettroneurografia#:~:text=L'elettromiografia%20(EMG)%2C,dal%20punto%20di%20vista%20funzionale.)
- [ECG](https://it.wikipedia.org/wiki/Elettrocardiogramma)
- [Anatomy of The DIY Heart Rate Monitor](https://pulsesensor.com/blogs/news/6326816-anatomy-of-the-diy-heart-rate-monitor) 
- [HC 06 per Arduino ](https://www.giuseppecaccavale.it/arduino/hc-06-bluetooth-arduino/)
- [Elettrodi Top Trace](https://www.elettromedicali.it/diagnostica/elettrocardiografi/elettrodi-monouso-per-ecg/prodotto-elettrodi-pregellati-in-foam-per-ecg-e-stress-test-36x42-mm-solid-ge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) 
- [HTTP POST](https://en.wikipedia.org/wiki/POST_(HTTP))
- [tempcontrol.it](https://github.com/mastroalex/tempcontrol)
- [Il manuale di Arduino](https://www.zeppelinmaker.it/il-manuale-di-arduino/?v=532773df6f8a)
- [Programmare](https://www.zeppelinmaker.it/programmare-2/?v=532773df6f8a)
- [PHP Pwd](https://www.mrw.it/php/pagina-protetta-password_11675.html)

## Authors 

- [Mastrofini Alessandro](https://www.linkedin.com/in/alessandro-mastrofini/)
- Rago Miriana
- Volpato Rebecca

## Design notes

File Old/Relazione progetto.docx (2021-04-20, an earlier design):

RELAZIONE PROGETTO CORSO DI ELETTRONICA 2

Docente:

Giancarlo Orengo

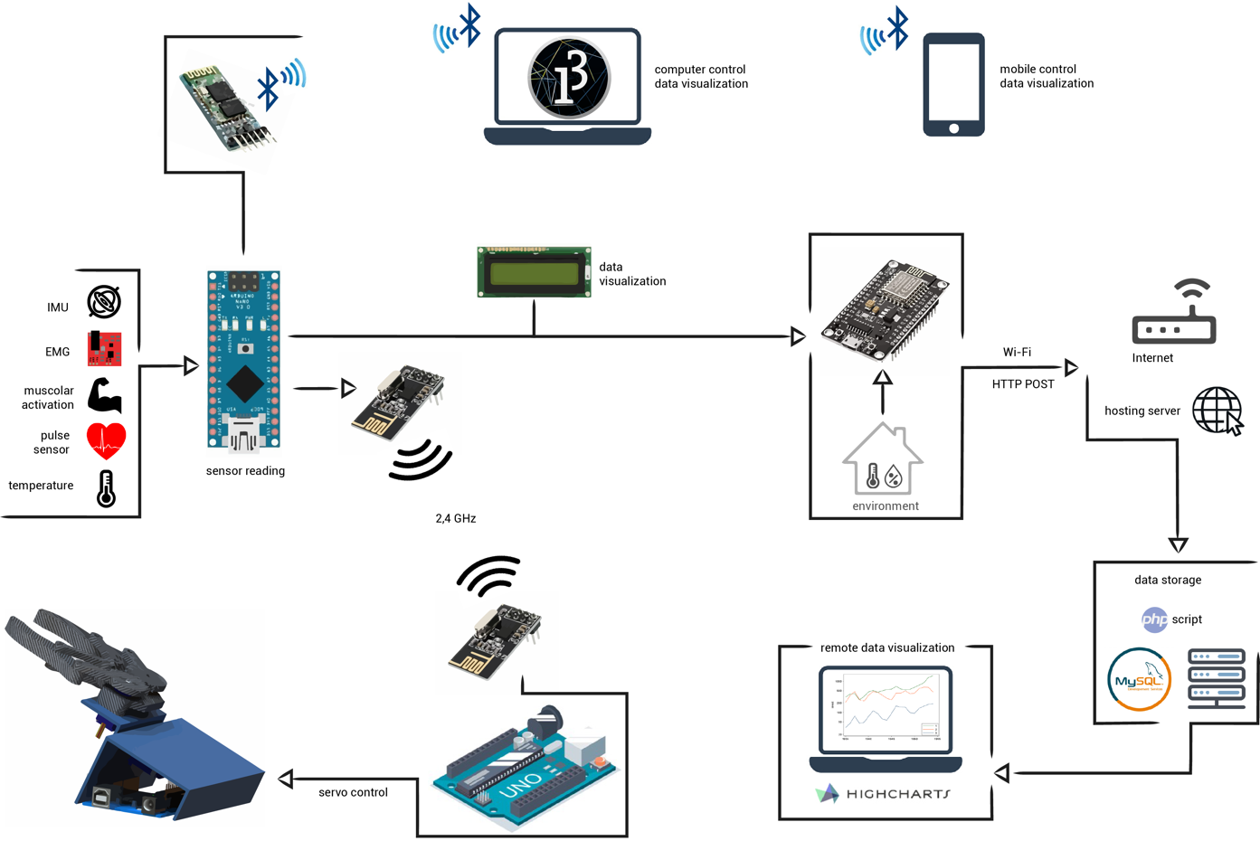
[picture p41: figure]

Ad opera di:

Mastrofini Alessandro

Rago Miriana

Volpato Rebecca

# Sommario

# Introduzione

Lo scopo del progetto è mostrare un’idea su come sia possibile controllare una pinza e la sua rotazione attraverso un segnale di alcuni sensori come un sensore inerziale e un’elettromiografia. La struttura è molto semplice e progettata nel pieno della filosofia Maker cercando di sfruttare oggetti di recupero con il solo scopo di mostrare come sia possibile controllare i movimenti indicati. Un esempio in Fig. 1.

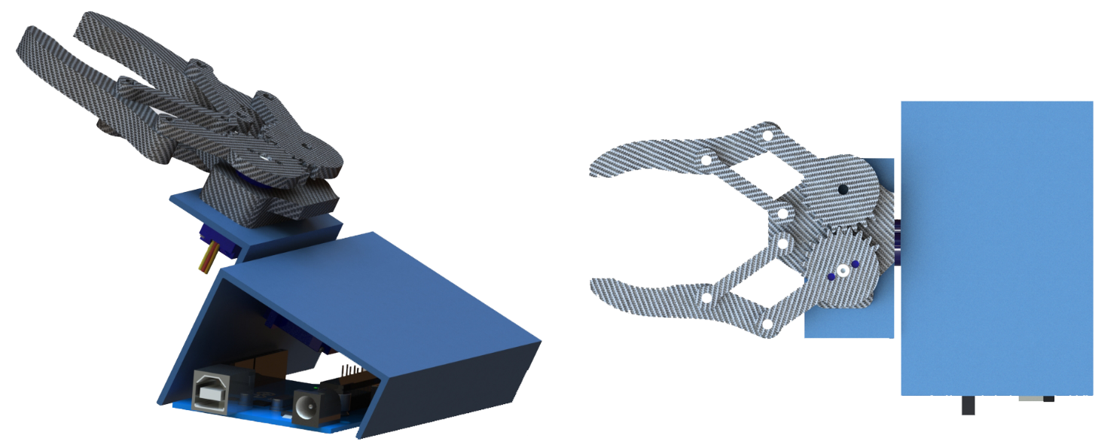
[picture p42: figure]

La pinza è stata poi molto semplificata e realizzata in diverse versioni ma lo stesso progetto può essere realizzato acquistando una pinza per robot dal costo di pochi euro. Una possibilità è quella di realizzarla con due ingranaggi connettendone uno al servomotore e di connettere le due braccia della pinza direttamente agli ingranaggi. Come mostrato in Fig. 2. L’architettura prevede diversi livelli. Si parte dal un Arduino Nano che leggere i sensori e fa una prima elaborazione del segnale ottenendo alcuni parametri sintetici che invia, attraverso una comunicazione radio a 2,4 GHz ad un Arduino Uno collegato ai due servo che muovo i servomotori.

Fig. 1 – Struttura di esempio della pinza per il controllo di apertura e chiusura e della rotazione.

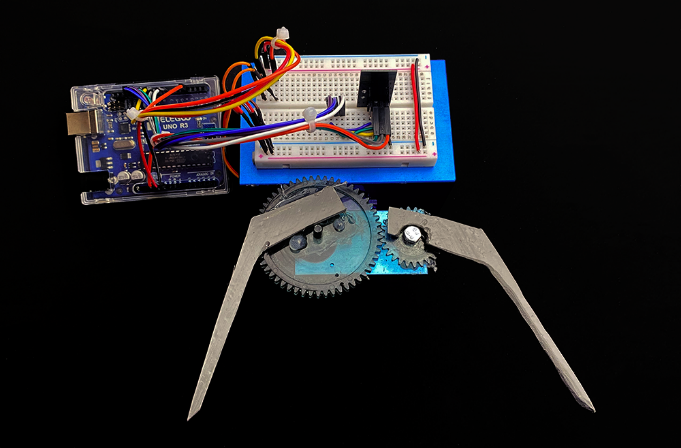
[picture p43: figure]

Fig. 2 – Esempio di struttura realizzata con gli ingranaggi, plastica sagomata e una base in alluminio anodizzato

L’Arduino Uno provvede anche a comunicare via Bluetooth sia con dispositivi mobile che con computer.

Inoltre, è stato aggiunto un modulo tramite un ESP 8266 che permette di raccogliere anche dati ambientali ed inviare il tutto su un server sotto un dominio di proprietà attraverso il quale è possibile salvare i dati e visualizzarli in remoto.

Sono stati utilizzati un sensore inerziale per leggere l’inclinazione del polso e controllare la rotazione della pinza, tale sensore include anche un sensore di temperatura che è stato sfruttato con l’idea di raccogliere la temperatura dell’utente. Inoltre, è stato utilizzato anche un sensore EMG per misurare l’attività muscolare in modo da regolare la chiusura della pinza.

# Dispositivi utilizzati

## GY-521

Il GY-521 è un modulo che permette di include un sensore MPU-6050 e un sensore di temepratura. MPU-6050 è un chip fabricato da Invesense [1], è un’unità di misura inerziale (IMU) basata sulla tencologia MEMS e contiene un accelerometro a tre assi e un giroscopio a tre assi uniti in un singolo chip. Questo sitema a 6 gradi di libertà (6 DOF) ci fornisce quindi 6 valori in uscita.

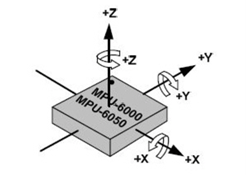
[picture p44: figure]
orientation_of_axes

Fig. 3 – Orientazione degli assi per il sensore inerziale.

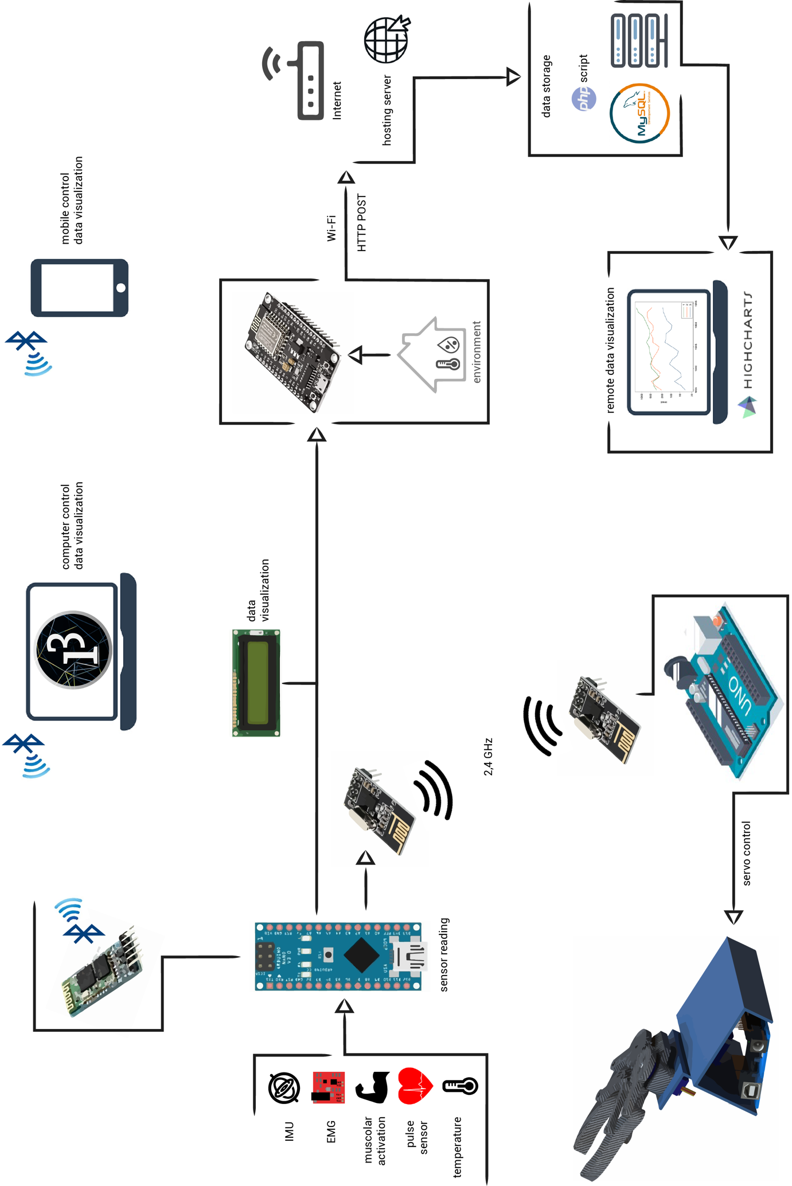
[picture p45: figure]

Fig. 4 – Architettura complessiva del progetto

# Riferimenti

[1] | Invesense, «MPU6050,» [Online]. Available: https://invensense.tdk.com/products/motion-tracking/6-axis/mpu-6050/.

# Indice delle figure

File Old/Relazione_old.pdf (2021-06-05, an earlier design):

# RELAZIONE PROGETTO CORSO DI ELETTRONICA 2

Docente:

## Giancarlo Orengo

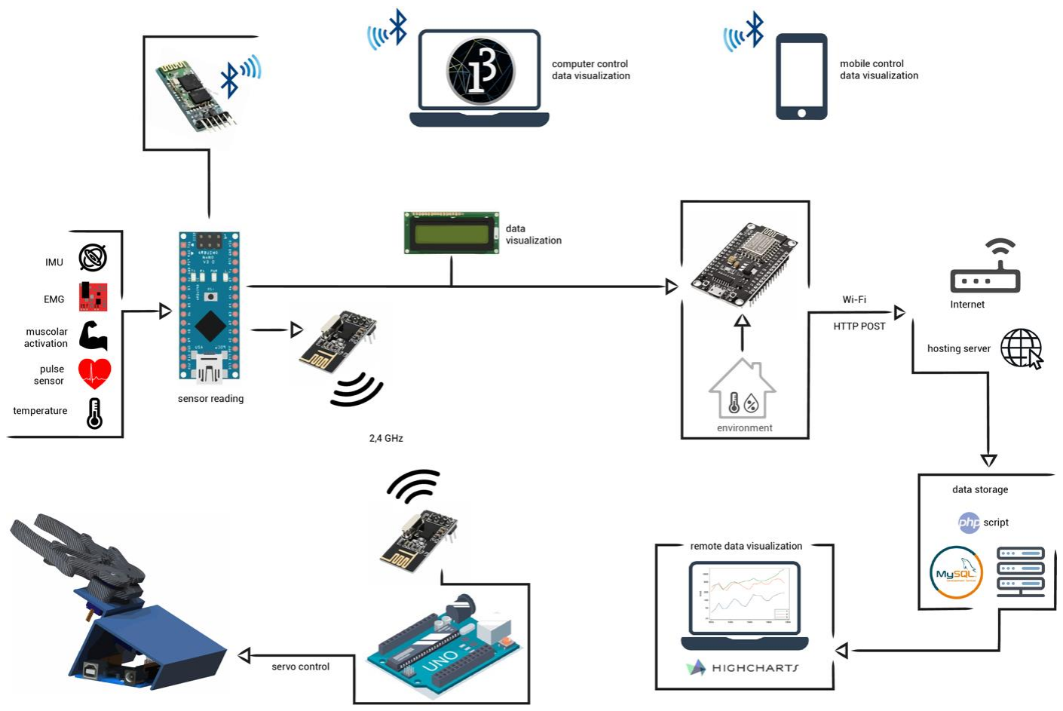
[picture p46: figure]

Ad opera di:

## Mastrofini Alessandro

## Rago Miriana

## Volpato Rebecca

## Sommario

## Introduzione

Lo scopo del progetto è mostrare come sia possibile controllare una pinza e la sua rotazione attraverso un segnale di alcuni sensori come un sensore inerziale e un sensore per l’elettromiografia. La struttura è molto semplice ed è stata progettata nel pieno della filosofia Maker cercando di sfruttare oggetti di recupero con il solo scopo di mostrare l’idea che c’è dietro. Un esempio in Fig. 1.

La pinza è stata realizzata in tre modi diversi, ma lo stesso progetto può essere realizzato acquistando direttamente una pinza per robot. Una possibilità è quella di realizzarla con due ingranaggi, connettendone uno al servomotore e collegare le due braccia della pinza direttamente agli ingranaggi. Come mostrato in Fig. 2.

L’architettura complessiva del progetto prevede diversi livelli. Si parte da un Arduino Nano che deve leggere i sensori e fa una prima elaborazione del segnale ottenendo alcuni parametri sintetici che invia, attraverso una comunicazione radio a 2,4 GHz ad un Arduino Uno a cui sono collegati i due servo che muovo la pinza.

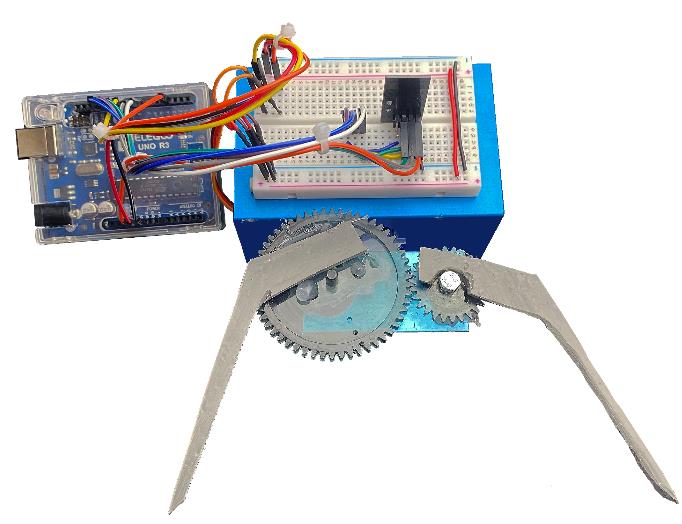
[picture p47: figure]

Fig. 2 – Esempio di struttura realizzata con gli ingranaggi, plastica sagomata e una base di alluminio anodizzato.

L’Arduino Uno provvede anche a comunicare via Bluetooth sia con dispositivi mobile che con il computer.

Inoltre, è stato aggiunto un modulo, un ESP 8266 che permette di raccogliere i dati ed inviarli su un server sotto un dominio di proprietà attraverso il quale è possibile salvare i dati e visualizzarli da remoto.

Sono stati utilizzati un sensore inerziale per leggere l’inclinazione del polso e controllare la rotazione della pinza, tale sensore include anche un sensore di temperatura che è stato sfruttato con l’idea di raccogliere la temperatura dell’utente. Inoltre, è stato utilizzato anche un sensore EMG per misurare l’attività

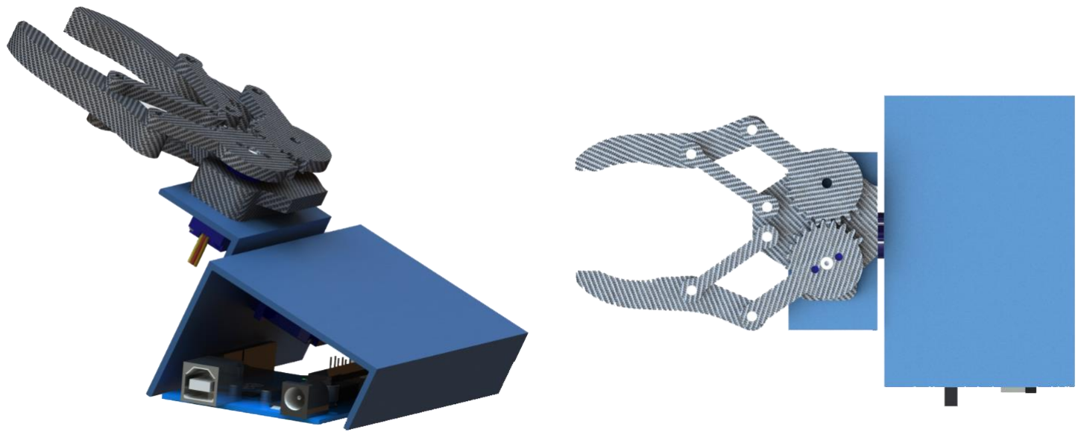
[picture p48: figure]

Fig. 1 – Struttura di esempio della pinza per il controllo di apertura e chiusura e della rotazione muscolare in modo da regolare la chiusura o l’apertura della pinza.

Proponiamo di seguito le altre due modalità di costruzione della pinza. Una possibile realizzazione della pinza può essere effettuata utilizzando il compensato Fig. 3. Per la progettazione si parte dal disegno dei vari componenti sul compensato, si procede poi con il taglio e infine l’assemblamento. Sopra la base che supporta la pinza è stato montato l’Arduino Uno con il ricetrasmettitore, il modulo bluetooth e i due servo che controllano la rotazione e l’apertura- chiusura della pinza.

Anche in questo caso uno degli ingranaggi è stato collegato con un servo mentre la base che contiene la pinza e ne permette la rotazione è stata collegata all’altro servo.

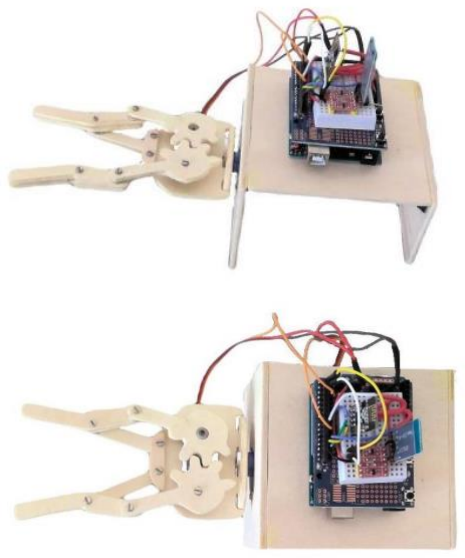
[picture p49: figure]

Fig. 3 – Modello della pinza in compensato

## Dispositivi utilizzati

GY-521

Il GY-521 è un modulo che permette di includere un sensore MPU-6050 e un sensore di temperatura. MPU-6050 è un chip prodotto da Invesense [1], è un’unità di misura inerziale (IMU) basata sulla tencologia MEMS che contiene un accelerometro a tre assi e un giroscopio a tre assi all’interno di un un singolo chip. Questo sitema a 6 gradi di libertà (6 DOF) fornisce quindi 6 valori in uscita.

Fig. 4 – Orientazione degli assi per il sensore inerziale.

L’accelerometro è in grado di rilevare l’accelerazione di un corpo lungo il proprio asse, mentre il giroscopio è in grado di rilevare la velocità angolare di un corpo su di un proprio asse. Il modulo GY-521 ha piccole dimensioni ma è molto preciso, contiene un chip con un convertitore analogico-digitale a 16 bit integrato per ogni canale e questo permette di catturare i canali X, Y e Z contemporaneamente. Il range di misura dell’accelerometro è +2, +4, +8, +16g, mentre il range di misura del giroscopio è ±250, 500, 1000 e 2000 °/s. Necessita inoltre, di una alimentazione da 3V a 5V.
Questo sensore utilizza il protocollo di comunicazione standard I²C, in particolare per la comunicazione è necessario importare due librerie una per l’I²C e una per la comunicazione con l’MPU-5060.

### Servo

Un Servomotore è un attuatore rotativo o lineare che consente un controllo preciso della posizione angolare o lineare, della velocità e dell’accelerazione.
È costituito da un opportuno motore accoppiato ad un sensore per il feedback di posizione. Richiede anche un controller relativamente sofisticato che spesso consiste in un modulo dedicato, progettato specificatamente per l’uso con i servomotori.

In questo progetto è stato usato il Microservo SG90. Può ruotare approssimativamente di 180° (90° per entrambe le direzioni) e funziona esattamente come i servomotori standard ha solo delle dimensioni ridotte.

Fig. 5 – Collegamento dei pin del servo.

La posizione “0” (impulso di 1,5 ms) è al centro, “90” (impulso di ~ 2 ms) è tutto a destra, “-90” (impulso di ~ 1 ms) è tutto a sinistra.

Per gestire facilmente il controllo PWM viene utilizzata la libreria Servo.

Invece, per controllare il servo è stato utilizzato il seguente comando:

Fig. 6 – Schema di collegamento del servo e dell’IMU (sensore inerziale).

### Sensore EMG

Il sensore per l’EMG, dove EMG sta per Elettromiografia [2], è un sensore in grado di misurare l’attività muscolare monitorando il potenziale elettrico generato dalle cellule muscolari. L’elettromiografia nasce per la ricerca medica e per la diagnosi dei disturbi neuromuscolari. Tuttavia, i sensori per l’EMG oggi vengono utilizzati nella robotica e in altri sistemi di controllo.

L’EMG valuta lo stato di salute dei muscoli e delle cellule (i motoneuroni) che li controllano. Queste cellule trasmettono segnali elettrici che provocano la contrazione e il rilassamento muscolare. Un EMG traduce questi segnali in grafici o dati e aiuta i medici ad eseguire una diagnosi.

Questo sensore amplifica ed elabora l’attività elettrica di un muscolo e lo converte in un segnale analogico che può essere letto da qualsiasi microcontrollore con un ADC, come Arduino.

Quando il muscolo sottoposto a misurazione si contrae, la tensione di uscita del sensore aumenta.

Fig. 7 – Segnale grezzo EMG prima di essere filtrato, rettificato e smoothed [3].

Collegato al sensore, tramite un connettore jack da 3,5 mm, c’è un cavo che da un lato è collegato ad Arduino, mentre dall’altro lato termina con tre connettori a clip che si attaccano a tre elettrodi.

In questo progetto è stato usato il Muscle Sensor V3 [4]. Questo sensore necessita di una tensione di riferimento positiva ed una negativa, quindi sono richieste due batterie da 9V.

Fig. 8 – Schema di collegamento dei pin del sensore.

L’Output Signal richiede un pin analogico, in particolare è stato utilizzato il pin A0.

L’EMG di superficie può essere registrato da una coppia di elettrodi o da una matrice più complessa di elettrodi. È necessario più di un elettrodo perché le registrazioni dell’EMG mostrano la differenza di potenziale tra due elettrodi separati.

Come si può leggere nel datasheet o nello schema elettrico, il segnale dei due elettrodi entra in un amplificatore per strumentazione:

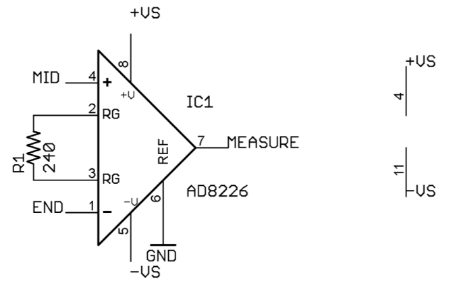
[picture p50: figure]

Fig. 9 – Schema dell’amplificatore per strumentazione.

Successivamente il segnale viene rettificato:

Fig. 10 – Raddrizzatore a doppia semionda che permette di rettificare il segnale amplificato.

Alla fine, il segnale viene ripulito attenuando rumori generati da artefatti ambientali, elettrici, elettronici, fisiologici ecc.

Fig. 11 – Smoothing, filtro attivo passa basso.

In sintesi, si ottiene un segnale proporzionale alla contrazione muscolare che verrà inviato all’ADC di Arduino.

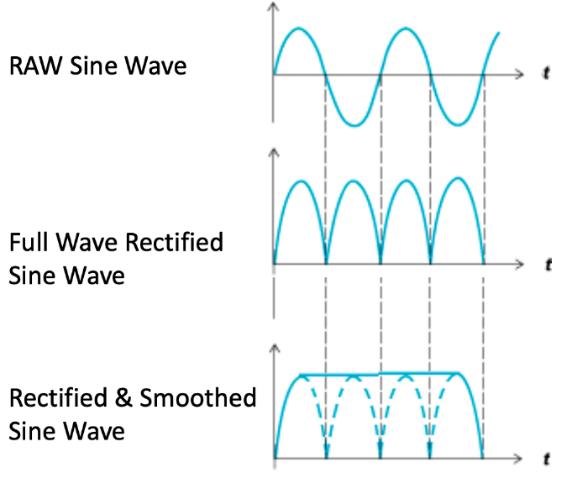
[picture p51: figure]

Fig. 12 – Raw EMG vs EMG dopo il raddrizzatore a doppia semionda e lo smoothing.

Il Muscle Sensor V3 è fuori produzione, quindi per il progetto è stata acquistata una copia del sensore. Questa copia risulta più economica tuttavia presenta alcuni difetti. Il sensore, infatti emette un segnale senza livellamento e pieno di disturbi.

Fig. 13 – Copia del Muscle Sensor V3 utilizzata nel progetto.

### Elettrodi

L’attività elettrica di un muscolo viene rilevata con l’ausilio degli elettrodi per l’EMG. Ci sono differenti tipi di elettrodi, in questo progetto sono stati utilizzati gli elettrodi di superficie, in particolare quelli in gel [5, 6]. Questo tipo di elettrodi contiene un gel elettrolitico come interfaccia tra gli elettrodi e la pelle.

Gli elettrodi gelificati forniscono una tecnica non invasiva per la misurazione e il rilevamento del segnale EMG, ma sono generalmente utilizzati per i muscoli di superficie poiché vengono applicati sulla pelle.

Gli elettrodi devono essere applicati in modo appropriato, in particolare, due elettrodi devono essere posizionati tra l’unità motoria e l’inserzione tendinea del muscolo, lungo la linea longitudinale del muscolo. La distanza tra il centro dei due elettrodi dovrebbe essere di 1-2 cm.

Il connettore a clip rosso va posizionato sull’elettrodo al centro del corpo muscolare, quello verde ad un’estremità del corpo muscolare e infine, il terzo connettore (giallo) deve essere posizionato su una sezione inattiva del corpo.

Fig. 14 – Posizionamento degli elettrodi.

È importante fare alcune considerazioni sui segnali EMG.

La fonte elettrica è il potenziale di membrana muscolare di circa -90 mV. La frequenza di ripetizione tipica dell’impulso dell’unità muscolo-motoria è di circa 7-20 Hz, a seconda

della dimensione del muscolo i potenziali misurati variano tra meno di 50 µV fino a 30 mV. Questo significa che il segnale deve essere amplificato come è stato mostrato nel paragrafo precedente.

A causa della bassa qualità del circuito EMG, il segnale analogico acquisito è risultato pieno di rumore. La tensione è stata solo rettificata ma non molto livellata, quindi è stato utilizzato un semplice algoritmo di livellamento riportato in Appendice A.

Quanto riportato in Arduino’s reference smoothing script [7] è lo script di smoothing di riferimento di Arduino che è stato utilizzato apportando piccole modifiche dopo un lungo periodo di test. In Fig. 15 si può osservare il segnale nel Plotter seriale di Arduino, in cui sono stati riportati il segnale grezzo, un valore soglia e il segnale ripulito.

Questa media livellata consente di personalizzare il codice riportato in Appendice B per controllare il servo che permette l’apertura e la chiusura della pinza.

### Pulse Sensor

Il principio di questo sensore è quello di puntare una luce tra le dita, la quale viene assorbita o riflessa e una parte passerà attraverso i tessuti più sottili. Quando il sangue viene pompato attraverso il corpo, viene schiacciato nei tessuti capillari e il volume di quei tessuti aumenta leggermente, quindi tra i battiti del cuore il volume diminuisce. La variazione del volume influisce sulla quantità di luce che verrà trasmessa. Questa fluttuazione è molto piccola ma può essere percepita con l’elettronica.

Si inizia con una sorgente e un rilevatore di luce. Si utilizzano un LED a infrarossi e un fotodiodo. La luce infrarossa viene assorbita dal sangue e riflessa dai tessuti circostanti, tale assorbimento è dovuto alla presenza dell’emoglobina nel sangue [8]. È importante che i due dispositivi siano accoppiati correttamente, così che la lunghezza d’onda della luce emessa dal LED venga rilevata dal fotodiodo. Il fotodiodo consiste di una giunzione che genera una piccola corrente quando viene bombardato con i fotoni.

A questo punto è necessario amplificare il segnale che esce dal fotodiodo e questo è possibile grazie ad un circuito che è il Convertitore corrente tensione. In Fig. 16 è riportato lo schema circuitale completo del sensore.

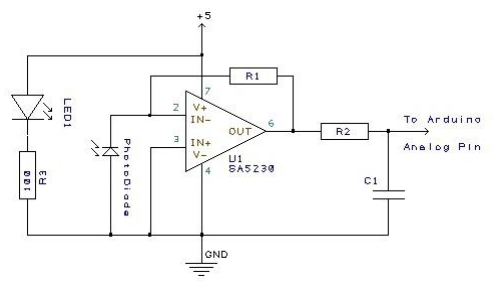
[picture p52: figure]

Fig. 16 – Schema circuitale del Pulse Sensor [9].

Fig. 15 – Segnale smoothed (blu), segnale originale (verde), soglia (rosso). Quando il segnale è al di sotto del valore soglia l’arto è rilassato, mentre, quando il segnale è al di sopra della soglia il muscolo è contratto.

Il fotodiodo deve essere schermato dalla luce ambientale che genera molto rumore nel segnale. Infatti, come si può vedere in Fig. 18 il segnale del sensore è distorto anche da piccoli movimenti. Inoltre, qualsiasi disallineamento o movimento del LED a infrarossi confonderà il segnale.

Fig. 17 – Immagine del sensore. Il cavo rosso corrisponde ai 5V, il cavo nero al GND e il cavo viola è il segnale.

Pulsesensor.com produce un sensore [10] che è abbastanza piccolo da poter essere indossato comodamente in diverse configurazioni ed è immune al rumore. È costituito da un circuito integrato di dimensioni ridotte che ha combinati al suo interno un fotodiodo e un circuito op-amp. Le dimensioni ridotte hanno come risvolto il fatto che è possibile mantenere un contatto stretto e costante con la pelle. Questo di fatto protegge il sensore dai cambiamenti della luce ambientale e riduce al minimo i rumori dovuti al movimento.

Il segnale grezzo è quello in Fig. 18.

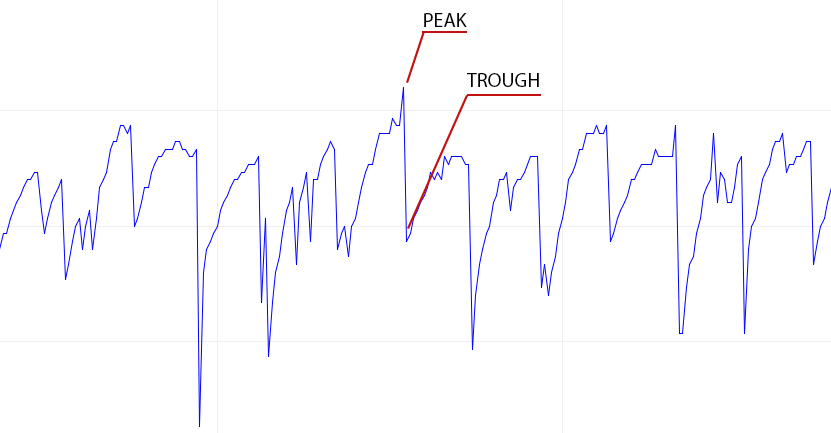
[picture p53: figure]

Fig. 18 – Picco e depressione del segnale grezzo.

Per le prime prove con il sensore su Arduino è stata utilizzata la libreria PulseSensor Playground, tuttavia questa non è risultata completamente compatibile con le altre funzionalità che sono state implementate successivamente. Quindi è stata eliminata la libreria ed è stato scritto un codice apposito.

La lettura è richiamata dalla funzione battiti() descritta nella libreria funzioniBPM.h.

Sono state messe insieme idee prese da Instructables [11] e da Pulsesensor [10] per ottenere un codice che si occupi di leggere il valore analogico e identificare il battito al di sopra di una certa soglia. Il codice è relativamente complesso. Oltre ad una parte deputata a stampare i simboli o una frase affermativa quando un battito viene rilevato, il Timer 2 viene utilizzato per impostare un interrupt ogni 2 ms. Una parte di codice più complessa si occupa di misurare il tempo trascorso dall’ultimo battito e di fare campioni appropriati per evitare il rumore. In particolare, si cerca di evitare il rumore dicrotico e di rilevare i picchi. Quando viene rilevato un battito (un picco conforme alle condizioni imposte) il valore del tempo viene aggiornato e vengono calcolati i BPM e il numero di battiti che possono verificarsi in 1 minuto (60000 ms).

Le funzioni primarie sono svolte da ISR(TI-MER2_COMPA_vect) e battiti() e serialOutputWhenBeatHappens() che si occupa di restituire il valore del battito.

### Test dei sensori

Nella Fig. 19 è riportato il circuito che mostra la configurazione del test per lo sviluppo del codice iniziale.

Questa configurazione in Fig. 19, con due batterie da 9 V consente di avere +9 e -9 V sui terminali Vs del sensore per l’EMG. È anche possibile utilizzare un alimentatore da 18 V DC e dividerlo in +9 e -9.

Questa configurazione è stata utilizzata per eseguire tutti i test dei dispositivi e del codice. È stato, in seguito, rielaborato parte del codice

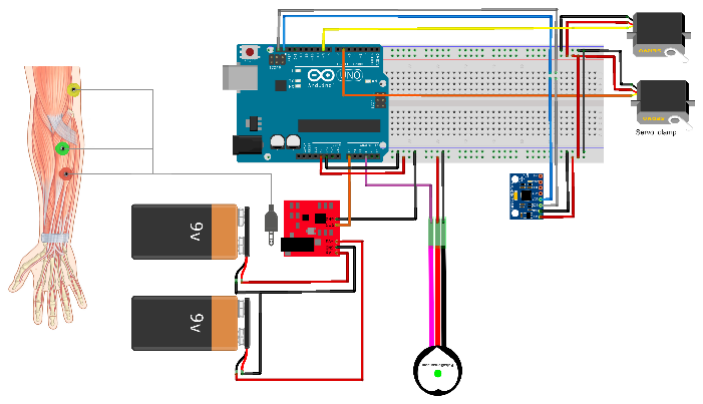
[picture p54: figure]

suddividendolo nei vari moduli in modo da avere un sistema più modulare che permettesse di aggiungere e rimuovere i dispositivi a seconda delle necessità. Da questa configurazione di partenza, sono stati suddivisi i diversi dispositivi in una struttura determinata per il monitoraggio e una struttura con gli attuatori.

Alla fine, i sensori che devono venire a contatto con il braccio e il polso sono stati uniti in un unico cavo dotato di connettore per collegarlo alla struttura di monitoraggio.

Tutto è stato quindi riorganizzato in modo più compatto.

## Divisione dei dispositivi

Come riportato nel paragrafo precedente dopo una serie di prove con i diversi sensori i dispositivi utilizzati sono stati separati e i codici sono stati riorganizzati. In particolare, è stato sfruttato un Arduino Nano per la lettura dei sensori e un Arduino Uno per controllare i servomotori.

La comunicazione tra i due Arduino avviene tramite radio utilizzando due ricetrasmettitori NRF24L01 [12] da 2.4 GHz.

Fig. 20 – Modulo NRF24L01 e schema di collegamento dei pin.

Questo dispositivo ha una tensione operativa di 1.9V ÷ 3.6V, un’antenna di 2,4 GHz incorporata e una velocità operativa (massima) di 2Mbps. Il chip è gestito dall’interfaccia SPI. Tramite questa interfaccia è possibile accedere ai registri del chip e modificarne tutti i parametri.

Questa operazione complessa, però, è facilitata dall’utilizzo delle librerie.

Il collegamento del modulo richiede l’utilizzo di diversi pin:

- GND
- Vcc, il modulo utilizza 3.3V
- CE, Chip Enable, utilizzato per abilitare la comunicazione SPI
- CSN, Chip Select Not, un pin che deve essere sempre al livello alto altrimenti disabilita l’SPI
- SCK, Serial Clock, fornisce l’impulso di clock con il quale funziona la comunicazione SPI
- MOSI, Master Out Slave In, collegato al pin MOSI di Arduino, serve per il modulo, per ricevere dati da Arduino
- MISO, Master In Slave Out, collegato al pin MISO di Arduino, serve per il modulo, per inviare dati da Arduino.
- IRQ, è un pin basso attivo, viene utilizzato solo se è richiesto l’interrupt.

Per utilizzare questo modulo è necessario impostare la lettura o la scrittura nel setup() come segue:

Fig. 19 – Circuito con i diversi sensori utilizzati.

È anche importante definire i pin CE e CSN.

Per la trasmissione è stata utilizzata una funzione charfortransmission() creata ad hoc che permette di concatenare una lettera che indica quali dati vengono trasmessi e il valore assunto dalla variabile corrispondente. Questa funzione viene ripetuta nel loop() del codice principale e viene continuamente chiamata per inviarle parametri diversi a seconda della variabile. All’interno della funzione i parametri da inviare devono essere prima convertiti in char per consentire la corretta trasmissione con le librerie utilizzate.

Il ricevitore ha una funzione simile, radionuovo(), che per prima cosa analizza il primo carattere identificando quali informazioni vengono ricevute e inserisce i dati nelle variabili corrispondenti dopo aver effettuato le opportune conversioni sul tipo di variabile.

### Arduino nano per il rilevamento

Si può osservare in Fig. 21 la configurazione dell’Arduino Nano con i sensori sulla breadboard per la fase di test.

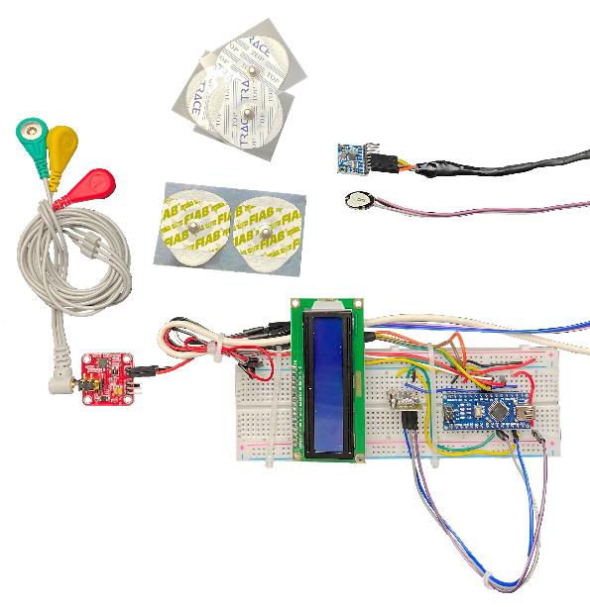
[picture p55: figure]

Fig. 21 – Disposizione dei sensori e dell’Arduino nano sulla breadboard.

Per l’Arduino Nano dedicato ai sensori, il circuito è stato modificato aggiungendo un display LCD per monitorare i parametri oltre al modulo NRF24L01 per la trasmissione radio. Il display LCD è collegato ad un modulo di interfaccia I²C per semplificare la comunicazione e la gestione dei cavi. Si può anche fare a meno del modulo di interfaccia I²C andando a collegare il display ai rimanenti pin dell’Arduino Nano, in tal caso saranno necessari 6 pin digitali, in particolare in questa configurazione possono essere utilizzati i pin (9, 10, 2, 3, 4, 5).

Per il resto la connessione dei sensori è rimasta invariata.

Come già riportato nei paragrafi precedenti l’utilizzo dell’Arduino Nano permette di rendere il tutto più compatto. La disposizione dei pin dei diversi sensori rimane la stessa, l’unica accortezza riguarda il fatto che non ci sono i pin dedicati SDA e SCL ma sono sui pin A4 e A5 come è possibile osservare in Fig. 22.

Fig. 22 – Disposizione e definizione dei pin su Arduino Nano [13].

Nel codice relativo a questa parte che coinvolge i diversi sensori la sezione relativa ai servomotori è stata rimossa e il resto è stato riorganizzato.

Il codice principale è riportato in Appendice C.

In particolare, il codice principale è stato semplificato aggiungendo diverse funzioni che chiamano definizioni di librerie esterne:

averagecalc() è stata definita in EM-Gsmooth.h e viene utilizzata per calcolare la media del segnale distorto.

printatore(LOW) è una funzione speciale che può essere usata per stampare il segnale EMG per il plotter seriale in modo da eseguire il debug di eventuali problemi di rilevamento. Di solito viene utilizzato per stampare tutti i valori sul monitor seriale. È definito in printerfunzioni.h

lcdprint() viene utilizzata per stampare i diversi valori e i relativi simboli sul display LCD.

battiti() è usato per rilevare i battiti cardiaci. È stato definito nelle funzioni funzioniBPM.h

charfortransmission() per la trasmissione dei dati con le relative informazioni.

Per mantenere il codice chiaro queste funzioni sono state definite in librerie esterne. La libreria EMGsmooth.h è responsabile del livellamento del segnale EMG al fine di ottenere precisione nella determinazione della soglia. La libreria funzioniBPM.h è già stata descritta nel paragrafo del sensore di battito. Il printerfunzioni.h contiene la funzione per stampare nel monitor seriale e nel display lcd, contiene anche la definizione del simbolo freccia e cuore sul display LCD.

Per creare caratteri speciali per LCD viene utilizzato LCD Custom Generator [14] che permette di generare un byte personalizzato con la definizione dei pixel ON ed OFF. Questo consente di usare simboli speciali oltre ai caratteri ASCII definendo individualmente i pixel di attivazione e disattivazione in una matrice 5x8 (byte_matrix). È possibile creare fino a 8 simboli diversi con la funzione createChar() della libreria LiquidCrystal e stamparli con lcd.Write(). Ad esempio, per il simbolo del cuore Fig. 24.

Fig. 24 - Creazione di caratteri speciali e disposizione dei valori sul display.

Ogni libreria contiene tutte le variabili e tutte le altre librerie necessarie al suo funzionamento.

Sono stati, quindi, ottenuti i seguenti valori che devono essere inviati all’Arduino con gli attuatori:

- tempmpu
- angolo
- media
- BPM
- soglia

Infine, è stato aggiunto anche un trimmer per controllare manualmente la soglia sul pin analogico A2.

### Arduino uno per l’esecuzione

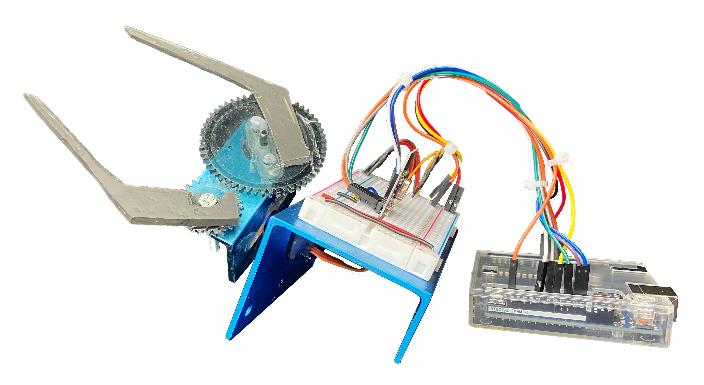
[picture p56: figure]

Fig. 25 – Configurazione dell’Arduino uno con i servo, il ricetrasmettitore e la pinza.

Questa seconda struttura si occupa di ricevere i segnali radio e ritrasmetterli via bluetooth (o via seriale) e di far muovere i due servomotori. È importante osservare che per aggiungere il modulo bluetooth, che verrà discusso nel paragrafo successivo, è stato utilizzato un convertitore di livello logico (Fig. 26) 3,3V – 5V TTL.

Fig. 26 – Convertitore di livello logico.

Bluetooth HC-06
Il modulo hc-06 riportato in Fig. 27 è un dispositivo che permette di trasformare un segnale sul bus seriale in un segnale bluetooth.

Fig. 27 – Modulo Bluetooth.

Tipicamente viene utilizzato un protocollo seriale software per comunicare, tuttavia in questo caso è stato utilizzato direttamente il bus UART sui pin TX e RX. Quindi, sono state create due nuove funzioni radioperbt() e decodserial(). La prima analizza il carattere ricevuto dall’NRF24L01 e a seconda della lettera ricevuta aggiorna la rispettiva variabile e contemporaneamente stampa il valore codificato nella seriale (quindi anche nel bluetooth). La seconda funzione, invece si occupa di analizzare i comandi ricevuti. Questa seconda parte verrà discussa meglio nella sezione GUI.

radioperbt() è stata originariamente scritta come una funzione per decodificare il messaggio radio e aggiornare le variabili (radionuovo()). Successivamente è stata aggiornata per consentire la comunicazione bluetooth inviando il messaggio codificato con la prima lettera che indica quale variabile corrisponde al dato.

La logica è quella di ricevere un array chart, analizzare il primo carattere e convertire tutti gli altri nelle variabili di interesse (float o int) e stampare nuovamente il messaggio come una Stringa codificata.

Servomotori
Per controllare i servomotori sono state create due funzioni.

pos_servo() è la funzione a cui viene passata l’inclinazione e si occupa di rimapparla correttamente per ruotare la struttura.

pinzacontrol() si occupa di far chiudere o meno la pinza in base al valore di soglia. C’è un ulteriore controllo prima di riaprire la pinza per evitare problemi dovuti alla fluttuazione del segnale.

Fig. 28 – Arduino Uno con i servo, il convertitore di livello logico, il modulo NRF24 e il modulo bluetooth.

## GUI

Nel progetto è stata sviluppata anche un’interfaccia grafica che consente di visualizzare i dati trasmessi e di prendere il controllo della pinza, sia dal computer che dallo smartphone.

### Processing and computer app

Per sviluppare l’interfaccia grafica sul computer è stato utilizzato Processing, compatibile con MacOs, Windows e Linux.

È riportata di seguito una breve descrizione dei vari elementi che costituiscono la finestra grafica.

Sliders
Per creare gli slider non sono state importate librerie, infatti gli elementi che creano gli slider sono stati disegnati con un programma di grafica e poi importate come immagini nella cartella del programma.

Una volta caricate le immagini nel codice, nella sezione draw sono state incollate nella finestra grafica.

Quando il mouse è premuto e il cursore si muove lungo la coordinata x per la lunghezza dello slider, l’indicatore seguirà il mouse simulando la funzione dello slider. Lo stesso per il secondo slider.

Le prime prove sono state effettuate utilizzando la libreria Firmata, alla fine questa libreria non è più stata utilizzata ma è stato inviato il comando con l’angolo di apertura o chiusura della pinza mappando i valori nello slider.

Grafico
Per poter visualizzare i dati provenienti dall’EMG è stato creato un grafico in cui è possibile visualizzare il trend di valori registrati.

La costruzione del grafico parte dal disegno degli assi, questo avviene tramite la funzione line(x1, y1, x2, y2) i cui valori indicano la posizione in cui è stato collocato il grafico e

Fig. 29 – Interfaccia grafica Processing anche la lunghezza degli assi; l’asse x è il tempo mentre l’asse y è l’ampiezza V delle oscillazioni dell’EMG.

All’interno di setdati() è stato definito un vettore di 1000 elementi e attraverso un ciclo for si accede agli elementi del vettore che sono i valori dell’EMG mappati tra 0 e 300 (l’altezza dell’asse y). È stato definito poi un altro vettore che contiene lo stesso numero di elementi del precedente e di nuovo si accede agli elementi tramite un ciclo for. È stata definita una variabile float chiamata passo che corrisponde alla lunghezza dell’asse x diviso il numero di campioni (data.lenght). Il valore assunto dall’elemento i-esimo del vettore datax[i] corrisponde a 50 + i ⋅ passo e questo vettore permette di individuare la coordinata x per costruire la linea che rappresenta l’andamento dell’EMG.

Una volta che è stata definita la relazione tra i dati ricevuti e l’asse x è possibile disegnare la linea tra due punti consecutivi. Questo è stato realizzato tramite la funzione line(datax[i], 650-data[i], datax[i+1], 650-data[i+1]).

Una volta che la curva raggiunge la fine dell’asse x, ricomincia dall’origine. La direzione degli assi è indicata dalla punta della freccia che è stata creata tramite la funzione triangolo composta da 6 valori che rappresentano le coordinate dei tre vertici del triangolo.

Switch
Lo switch è stato aggiunto per commutare i comandi, così da rendere possibile il controllo della pinza tramite gli slider presenti nell’interfaccia grafica.

Lo switch è stato creato prendendo spunto dagli esempi della libreria Cp5 che è stata importata nel codice.

Nella classe Serialcomunication è stata creata la funzione serialsend() in cui se il controllo manuale risulta attivo (if (pulsante == true)), se il mouse è premuto e si trova in corrispondenza di uno dei due slider, in base a quale slider verrà attivato la pinza potrà aprirsi/chiudersi oppure ruotare e questo risulta possibile mappando la posizione sullo slider in un range compreso tra 0° e 180° per la pinza e tra -90° e 90° per la rotazione. Questo valore viene in seguito scritto, come Stringa insieme ad un carattere identificativo, sulla porta seriale.

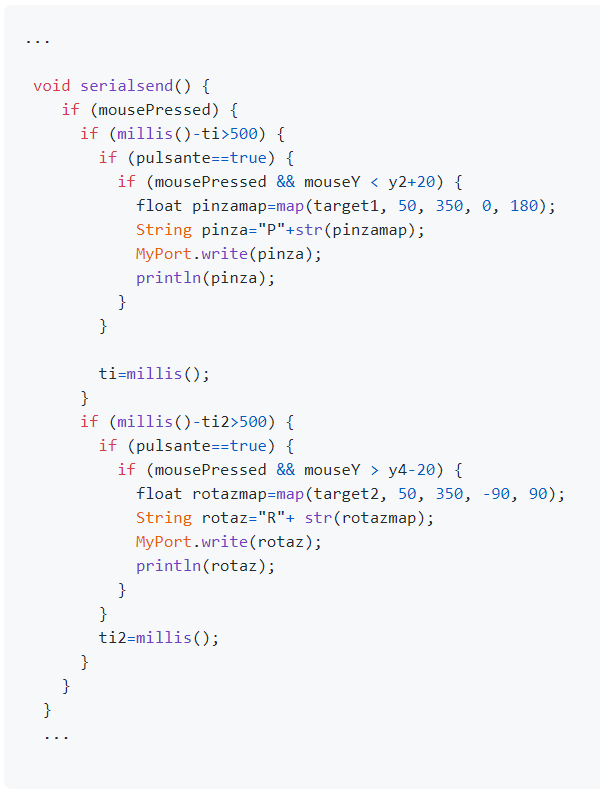
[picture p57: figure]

Cambiando lo stato dello switch, che di base è stato impostato con il valore false, si troverà quindi nello stato true e contemporaneamente verrà inviata la stringa “C1” sulla seriale, viceversa in corrispondenza dello stato false verrà inviata sulla seriale la stringa “C0”.

Quando viene letta la stringa “C1” dalla seriale la variabile booleana controlloapp viene portata ad 1 e questo corrisponde ad attivare il controllo manuale, ovvero permette di gestire la pinza attraverso gli slider. Quando, invece, viene letta dalla seriale la stringa “C0” la variabile controlloapp è portata a 0 e la pinza è controllata dai valori provenienti dal sensore di inerzia e dal sensore per l’EMG.

Sono stati creati, inoltre, dei riquadri in cui è possibile visualizzare i valori provenienti dai sensori come la temperatura, l’inclinazione e i battiti. Per la temperatura è stato costruito anche un termometro.

Bpm
Per visualizzare il valore dei battiti è stata importata l’immagine di un cuore all’interno del quale viene scritto il valore. L’immagine è stata prima copiata nella cartella del programma, poi è stata caricata nel codice e infine incollata nella finestra grafica con la funzione image().

L’aggiornamento continuo dei valori dei battiti è reso possibile dalla funzione text() in cui viene mandata una stringa nfn(Batt, 0) che trasforma la variabile float Batt che contiene i valori dei battiti trasmessi via bluetooth dall’Arduino Uno in una stringa con zero cifre a destra del punto decimale.

Roll
Nel riquadro chiamato Roll, vengono visualizzati i valori dell’inclinazione del sensore di inerzia, che corrispondono ai valori di rotazione della pinza.

È stato creato semplicemente un rettangolo con la funzione rect() all’interno della quale sono stati riportati i valori aggiornati della variabile con la stessa modalità del battito, questa volta utilizzando la variabile Incl.

Termometro
Per creare il termometro è stato prima disegnato il bulbo con la funzione ellipse() che disegna una ellisse centrata in x, y e i semiassi corrispondono alla lunghezza e all’altezza. Il bulbo è stato poi riempito con il mercurio e questo è reso possibile dalla funzione fill(200, 0, 0) che restituisce una colorazione sulla scala del rosso.

Successivamente è stato costruito il termometro che è dato dall’unione di un arco di circonferenza e un rettangolo, quindi sono state utilizzate le funzioni arc() e rect(). La funzione arc() contiene diversi valori come la posizione x e y del centro, la larghezza e l’altezza ed infine l’angolo di partenza e di arrivo.

Una volta che sono stati disegnati il bulbo e il termometro la parte interna al termometro viene riempita con il mercurio fino ad una certa altezza che è determinata da una funzione che permette di variare l’altezza del mercurio in accordo al valore di temperatura ricevuto.

Di seguito sono riportate le spiegazioni relative al meccanismo del mercurio e della scala centigrada.

Mercurio
Per costruire la colonna di mercurio che segnala la temperatura rilevata è stata utilizzata la funzione map(tempC, 0, 50, 0, 175) che mappa la temperatura tra 0 e 50 gradi nell’altezza della scala graduata. Poi h = -y-66 corrisponde all’offset tra lo zero e il bulbo.

Scala centigrada
In questa parte del codice è stata costruita la scala centigrada formata da una tacca più grande ogni 10 gradi e una più piccola a metà di ogni due tacche grandi.

Inizialmente sono state disegnate le tacche più grandi, quelle ogni 10 °C. È stato utilizzato un ciclo for da 0 a 5. Il disegno delle tacche è stato fatto tramite il comando line(), le due x del comando rappresentano la lunghezza della tacca, mentre le due y del segmento sono uguali e dipendono dal valore dell’indice.

Successivamente sono state disegnate le tacche più piccole con la stessa logica. La larghezza delle tacche diminuisce, in particolare è la metà delle precedenti, mentre per le y il ragionamento è analogo al precedente.

line(x inizio tacca, y, x fine tacca, y)

Il codice completo è riportato nell’Appendice E.

Decodifica bluetooth
Il Bluetooth svolge due importanti funzioni, la prima riguarda il passaggio al controllo manuale.

All’attivazione dello switch viene inviato un comando codificato Cx, dove x rappresenta lo stato del sistema. Se è 1 allora il controllo sarà manuale altrimenti sarà lasciato ai sensori.

Oltre ad inviare questo comando vengono inviati anche i valori angolari dei servomotori che verranno ricevuti, decodificati e implementati dalle funzioni pos_servo2(angolo) e pinzacontrol2(angolo) nella struttura in cui sono presenti i servomotori. Per inviare questi comandi è stato creato un doppio controllo (come riportato nella sezione Sliders) controllando il mouse premuto sulle coordinate dello slider e da un timer non bloccante per evitare errori nel buffer seriale di ricezione.

La rotazione è mappata e codificata con P per la pinza e R per la rotazione angolare.

L’altra funzione importante è ricevere i dati di temperatura, rotazione ed elettromiografia.

Per fare questo è stata implementata la funzione serialreceive().

Questa funzione controlla i dati in ingresso e li converte in char array (un array di caratteri). Quindi controlla il primo elemento per decodificare i dati e converte il valore in un numero e aggiorna la variabile.

Codice
Per rendere il codice più scorrevole e funzionale, sono state create delle classi contenenti i vari elementi grafici e funzionali. Ci sono differenti classi per:
- Termometro
- Schermi virtuali per visualizzare i dati
- Slider
- Comunicazione bluetooth e seriale
- Controllo dello switch
- Grafico EMG

Le varie classi sono collegate in modo da scambiarsi le variabili più importanti.

All’interno di ogni classe sono stati creati vari oggetti per implementare le diverse funzioni. È molto interessante, ad esempio, come questi tre diversi oggetti vengono richiamati nella classe di visualizzazione dei dati.

Questo per disegnare e aggiornare i tre display virtuali.

In questo modo è stato ottenuto un codice finale molto più organizzato. Il codice è riportato in Appendice D.

### App per smartphone

Dopo aver sviluppato un’interfaccia grafica sul computer è stata sviluppata anche un’applicazione per smartphone tramite MIT App Inventor [15]. Questa applicazione ha permesso di sviluppare una app completa e funzionale ma allo stesso tempo semplice. Un limite di questa applicazione consiste nel fatto che può utilizzata solo su dispositivi Android.

Le funzionalità sono le stesse dell’app per computer ovviamente integrate con la portabilità e l’ubiquità dello smartphone.

Per sviluppare l’applicazione per prima cosa si devono aggiungere tutti i componenti necessari come il List Picker, i Label, gli slider, il Bluetooth Client, i Clock e i Bottoni.

Una volta selezionati i componenti, si creano i blocchi. I diversi blocchi sono stati creati separatamente, facendo di volta in volta test per verificarne la funzionalità. Solo alla fine la grafica è stata ultimata e perfezionata.

I primi blocchi necessari sono quelli che permettono di selezionare il Bluetooth MAC Address del modulo bluetooth (HC-05) e che quindi permettono l’accoppiamento tra lo smartphone e il bluetooth su Arduino.

Successivamente, per passare dal controllo automatico dei servo a quello manuale è stato creato un blocco con funzioni simili a quelle di uno switch che invia “C0” e “C1” con le stesse regole di codifica viste per Processing.

Quando il controllo manuale risulta attivato (appcontrol == true) è possibile inviare i relativi dati. In particolare, vengono inviati sulla seriale i valori angolari dell’apertura o chiusura della pinza e della sua rotazione. Per quanto riguarda la rotazione per simulare questa funzione è stato utilizzato il giroscopio integrato nello smartphone e il relativo valore è stato riportato in Button1. L’apertura o chiusura della pinza è invece controllata da uno slider.

Per ricevere i dati, invece, è necessario verificarne la disponibilità e salvare quanto ricevuto sul buffer della seriale in una variabile.

In base ai tipi di variabile proposti da MIT App Inventor è stato necessario dividere la stringa contenente i dati ricevuti in una lista. Questa lista, decode_text, contiene diversi elementi ciascuno dei quali rappresenta un nuovo dato aggiornato codificato. I diversi elementi sono stati, quindi, decodificati controllando il primo carattere e salvando il valore corrispondente nella rispettiva variabile. Per il codice consultare Appendice G.

A questo punto è stata utilizzata un’interfaccia grafica di prova Fig. 31 per verificare il funzionamento generale.

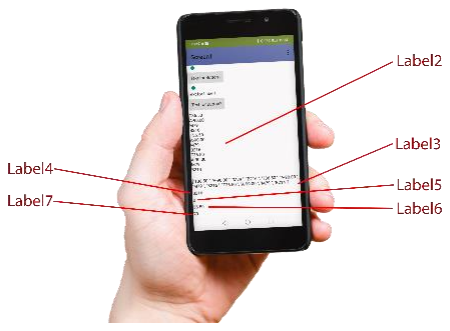
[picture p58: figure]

Fig. 31 – Interfaccia grafica di prova.

Dopo una serie di prove è stato ultimato il layout grafico e i blocchi sono stati riorganizzati. La struttura finale dei blocchi è riportata in Appendice H.

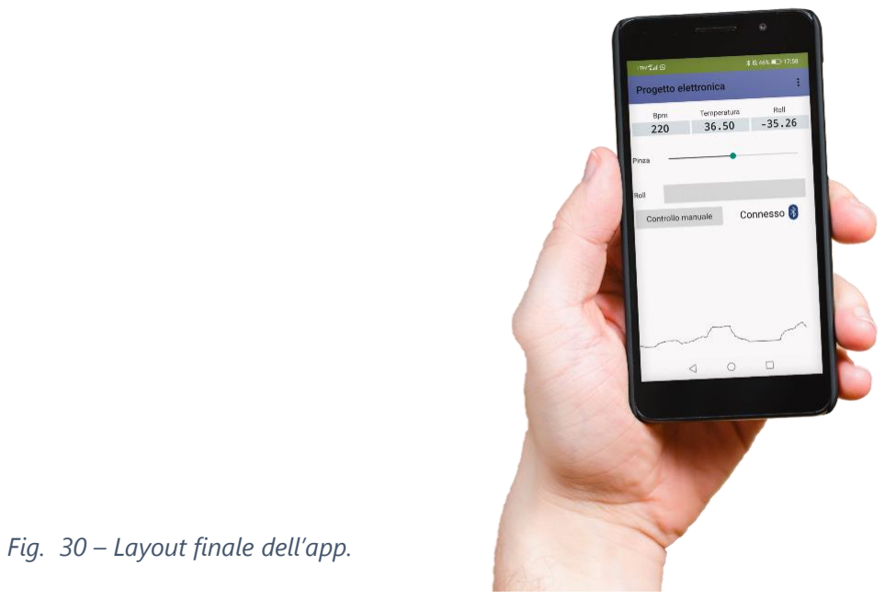
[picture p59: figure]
Fig. 30 – Layout finale dell’app.

## Registrazione e Archiviazione dei dati

Visto il recente interesse per la telemedicina è sembrato opportuno memorizzare i dati dell’esperimento direttamente in un server remoto, dando così la possibilità di visionarli da remoto e anche in tempi successivi.

Il circuito originale è stato, inoltre, integrato con un sensore di temperatura e umidità ambientale.

I dati vengono salvati su MySQL database raggiungibile da un dominio di proprietà di uno degli autori [16].

Per la visualizzazione dei dati sono state usate le librerie Highcharts [17], si tratta di una libreria software per la creazione di grafici dinamici scritta in puro JavaScript.

Di seguito sono riportati i dispositivi che sono stati utilizzati.

### ESP 8266

Il modulo Wi-Fi è stato aggiunto per permettere il salvataggio dei dati da remoto.
NodeMCU è una piattaforma open source sviluppata appositamente per l’IoT, include un firmware che funziona tramite il modulo Wi-Fi SoC ESP8266 e hardware con la base del modulo ESP-12E. Per comunicare con il computer utilizza un chip CH340.

La scheda è molto potente e avrebbe potuto sostituire l’Arduino Nano, tuttavia, è stato scelto di utilizzare l’Arduino per lasciare il sistema modulare con la possibilità di aggiungere o meno questa funzione.

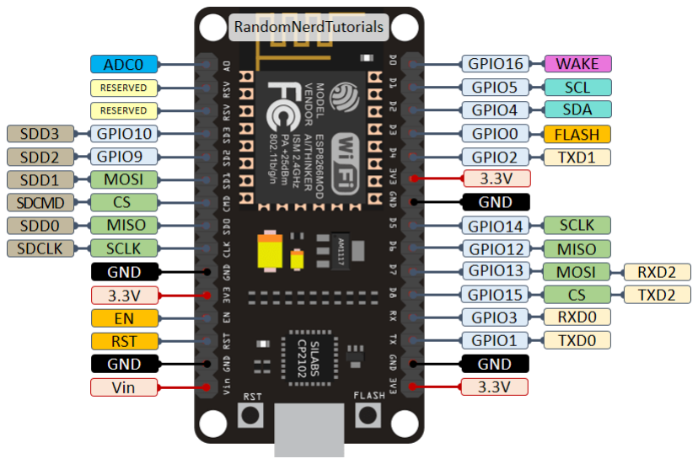
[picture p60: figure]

Fig. 32 – Pinout NodeMCU - Modulo Wi-Fi [18]

Per leggere i dati provenienti dall’Arduino nano, è stata implementata una software serial sui pin 3 e 4, trasmettendo i dati con la stessa logica di codifica utilizzata nei passaggi precedenti.

Dal lato dell’Arduino Nano si ha:

Passandogli i diversi parametri come transmit(“T”, String (tempmpu)).

Dal lato dell’ESP, invece, è stata inizialmente ripulita la stringa di caratteri di formattazione estrema (decodserial()) per poi passarla ad una seconda funzione che si occupa di trasformarla in un char array (process()) e infine la decodifica vera e propria aggiornando le variabili (analizestring()).

Inoltre, il dispositivo viene alimentato dai 5V di Arduino Nano questo per poterli accendere insieme.

È stato inoltre, implementato un software seriale su NodeMCU con una libreria dedicata.

Fig. 33 – Circuito con lo schema di collegamento del modulo Wi-Fi e del sensore di temperatura.

### DHT 11

Come riportato nel paragrafo precedente, è stato aggiunto anche un sensore di temperatura e umidità.

Il sensore DHT11 legge i valori utilizzando la libreria Adafruit per i sensori DHT.

È stato implementato in una libreria dedicata:

Di seguito è stato approfondito il discorso relativo alla memorizzazione dei dati in un server remoto.

### MySQL Database

Dal lato del server è stato creato un database dedicato con un utente personalizzato. Sono stati necessari i seguenti dati (nome_db e username) per implementare il codice nelle fasi successive.

Utilizzando phpMyAdmin è stata creata una tabella pronta a ricevere tutte le variabili di interesse:

### Richieste POST

Per inviare dati è stato utilizzato il metodo di richiesta HTTP POST [19]. Per impostazione predefinita, il metodo di richiesta POST richiede che un server Web accetti i dati racchiusi nel corpo del messaggio di richiesta, tipicamente per l’archiviazione.

È stato, quindi, collegato l’ESP 8266 ad Internet tramite la libreria Wi-Fi. È stato inoltre necessario includere una libreria per HTTP.

È stata, quindi implementata una funzione che invia ripetutamente un messaggio di testo contenente le variabili concatenate in una stringa che il server decodificherà in modo da posizionare correttamente i dati.

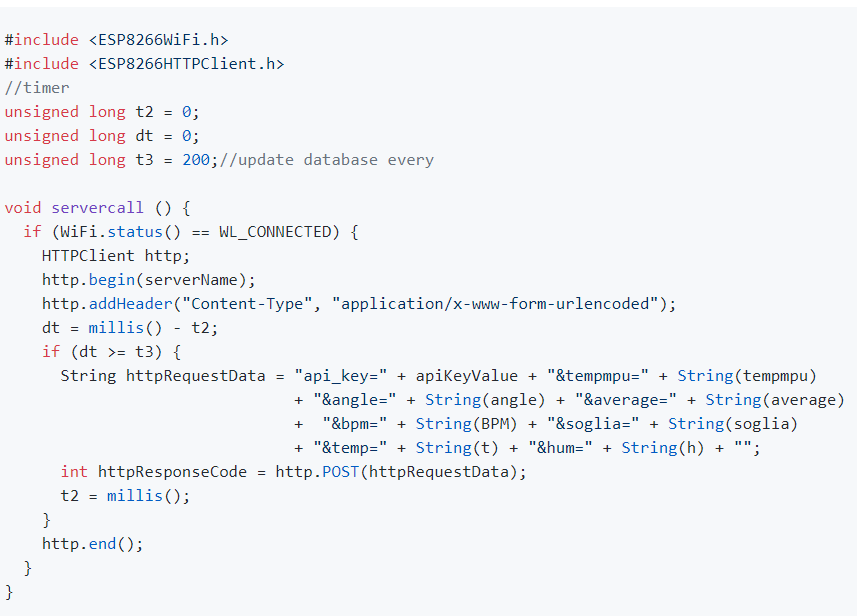
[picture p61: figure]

I dati sensibili come, per esempio, le password Wi-Fi e i nomi utente del database vengono salvate nel file sensdata.h.

Il codice principale è il seguente:

Una pagina php viene richiamata sul server e si occupa di decodificare i dati. La funzione si occupa di ricevere la stringa completa e di identificare le diverse variabili concatenate nell’ordine prescritto, collocandole poi nella colonna di riferimento all’interno della tabella. La funzione segna anche l’ora dell’inserimento.

Per il codice fare riferimento ad Appendice F.

### Visualizzazione dei dati

Per leggere i dati viene chiamata un’altra pagina php. Il codice è diviso in tre sezioni. La prima sezione si occupa di recuperare i dati dal database; la seconda si occupa delle strutture HTML e la terza si occupa dei grafici con l’aiuto delle librerie Highchart.

La pagina web con i dati è accessibile al seguente link http://tempcontrol.it/progelettronica/chart.php (http://tempcontrol.it/progelettronica/chart.php) o con questo short link: http://bit.ly/datiprogettoelettronica

La pagina web è protetta da una password con un algoritmo php [20], inserire elettronica.

Una pagina di struttura php è stata creata in diverse sezioni.

Una prima sezione di occupa della chiamata del database e della lettura degli ultimi valori. Anche questo è contenuto nel file call.php. Quindi salva i dati in variabili che verranno richiamate dai grafici. Ovviamente si tratta di vettori.

Poi c’è la struttura HTML in cui sono inseriti i diversi contenitori ognuno con un proprio stile per organizzare il layout.

Richiamando le variabili contenenti i dati, i grafici vengono costruiti utilizzando, come già scritto precedentemente, le librerie Highchart e quindi con un frammento di codice Java del tipo:

A questo si aggiunge un ulteriore algoritmo per proteggere la visualizzazione dei grafici con una password come mostrato in Appendice F.

I grafici sono ampiamente personalizzabili, in particolare, è stata attivata la possibilità di zoomare in un certo intervallo di tempo e di scorrere lungo l’asse del tempo. È anche possibile selezionare un singolo valore e leggere altre informazioni.

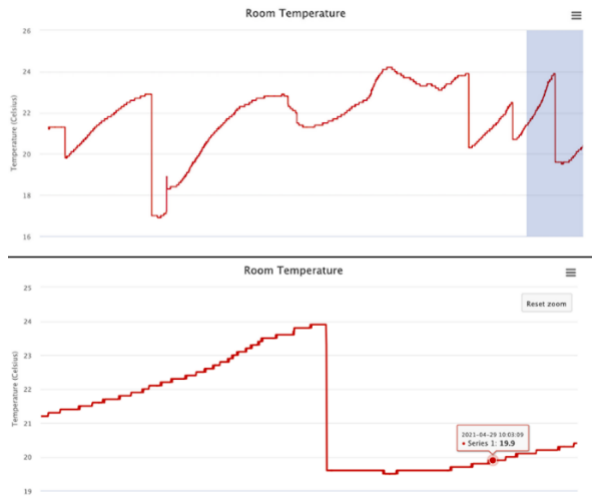
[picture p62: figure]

Fig. 35 – Esempio di un grafico con una regione zoomata riportata nella seconda figura.

## Come rendere tutto più compatto

Per rendere tutto più compatto ed evitare problemi dovuti alla mancanza di stabilità della breadboard è stato deciso di saldare il tutto su più schede millefori. Tuttavia, per consentire i test e la sostituzione dei componenti sono stati utilizzati anche connettori multi-pin.

### Cavo con i sensori

Per consentire un facile trasporto e smontaggio sono stati uniti tutti i sensori in un unico cavo.

L’EMG ha il suo cavo con jack da 3,5 mm.

È stato utilizzato un cavo Cat 5e con schema di cablaggio T568B. VCC e GND del pulsesensor e del sensore di inerzia sono stati uniti insieme e i dati del pulsesensor sono stati mandati sul pin A3.

I sensori sono stati collegati come segue:

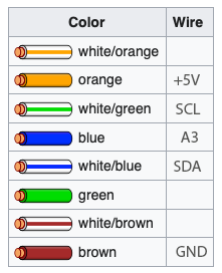
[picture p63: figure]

Fig. 36 – Tabella codice colore per l’assegnazione dei pin.

### Stazione di lettura

Per avere una struttura compatta ma che consentisse di effettuare diversi test, sono state impilate diverse schede millefori. Sono inoltre presenti un connettore jack femmina da 3,5 mm per il cavo dell’elettromiografia e un connettore RJ45 per il cavo del sensore. Al piano superiore sono presenti un display LCD e un trimmer per la regolazione della soglia.

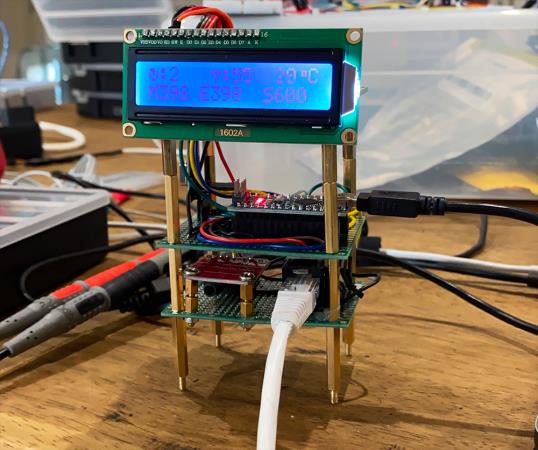
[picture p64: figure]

Fig. 37 – Stazione di lettura.

### Alimentazione

Per l’alimentazione vengono proposte due modalità diverse.

Nella prima sono stati utilizzati due diversi alimentatori da 9V, unendo un morsetto (+) con un (-) si ottiene un riferimento di massa in modo da avere +9V e -9V sugli altri due cavi.


Fig. 39 – Modifica degli alimentatori

Questo serve per alimentare il circuito dell’elettromiografia. È stato successivamente aggiunto un alimentatore da 12V per alimentare l’Arduino Nano da Vin che a sua volta alimenta l’ESP8266 e l’intero sistema. È stato quindi collegato il tutto alla base della stazione di lettura in modo da alimentare tutto con un unico cavo con connettore C13. Sono stati aggiunti, inoltre, due interruttori per accedere selettivamente al sistema e all’alimentazione per l’EMG.


Fig. 40 – Configurazione dello schema di alimentazione

Nella seconda è previsto l’utilizzo di due batterie da 9V per il sensore dell’EMG e due power bank per alimentare i due Arduino, senza dover ricorrere ad un computer con cavo USB.


Fig. 38 – Struttura finale della stazione di lettura dati.


## Conclusioni e sviluppi futuri

Il sensore di temperatura non riferisce perfettamente la temperatura del soggetto e potrebbe essere sostituito con un sensore a contatto con la pelle ed eventualmente studiato un algoritmo per riportare la temperatura periferica a quella centrale.

L’utilizzo di un sensore EMG più avanzato come il MyoWare [21] permette di ridurre i disturbi e avere una struttura più compatta.

Per sviluppare un’applicazione per iOS è necessario sostituire il modulo bluetooth con uno con Bluetooth Low Energy come il modulo SH-HC-08. Una prima bozza è stata discussa nella repository online di questo progetto.

Per aumentare la sicurezza dei dati in ottica di avere un rispetto della privacy e delle normative GDPR per il trattamento dei dati personali online, è sicuramente necessario provvedere ad un algoritmo di sicurezza molto più serio del semplice nascondere il contenuto della pagina con lo script php. Inoltre, potrebbe essere opportuno provvedere a una criptazione dei dati anche prima di inviarli al server e attivare il protocollo HTTPS nella pagina web.

Per la temperatura e umidità ambientali può essere opportuno sostituire il DHT11 con un

DHT22 ottenendo così una sensibilità di 0,5°C e 2% RH.

Per l’alimentazione, invece di tre alimentatori si potrebbe utilizzare un unico alimentatore da 18V con un voltage divider per ottenere ±9V.

Infine, la stazione di lettura potrebbe essere riprogettata su PCB in modo da avere un unico piano più compatto.

## Contenuti aggiuntivi

Per il video dimostrativo: youtu.be/k1hNBbgfAyE

A seguire un’Appendice in cui sono riportate le parti più interessanti di codice.

È possibile trovare un resoconto fatto passo passo con ulteriori dettagli, i codici completi e gli schemi di collegamento fritzing sulla repository: github.com/mastroalex/progelettronica (https://github.com/mastroalex/progelettronica)

Fig. 41 – Alternativa della stazione di lettura dati.

## Riferimenti

[1] Invesense, «MPU6050,» [Online]. Available: https://invensense.tdk.com/products/motion-tracking/6-axis/mpu-6050/.
[2] Wikipedia, «Elettromiografia ed elettroneurografia,» [Online]. Available: https://it.wikipedia.org/wiki/Elettromiografia_ed_elettroneurografia.
[3] A. Newton, «Electromyography(EMG) with MyoWare Muscle Sensor & Arduino,» [Online]. Available: https://how2electronics.com/electromyography-emg-with-myoware-muscle-sensor-arduino/.
[4] Advancer Technologies Shop, «Muscle Sensor v3,» [Online]. Available: http://www.advancertechnologies.com/p/muscle-sensor-v3.html.
[5] FIAB, «Elettrodi,» [Online]. Available: https://www.fiab.it/prodotti.php.
[6] Ram Apparecchi Medicali, «Elettrodi pregellati in FOAM per ECG e Stress Test 36x42mm,» TopTrace, [Online]. Available: https://www.elettromedicali.it/diagnostica/elettrocardiografi/elettrodi-monousoper-ecg/prodotto-elettrodi-pregellati-in-foam-per-ecg-e-stress-test-36x42-mm-solid-gel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.
[7] Arduino, «Smoothing,» [Online]. Available: https://www.arduino.cc/en/Tutorial/BuiltInExamples/Smoothing.
[8] ROHM, «Pulse sensor,» [Online]. Available: https://www.rohm.com/electronics-basics/sensor/pulsesensor.
[9] pulsesensor.com, «Anatomy of The DIY Heart Rate Monitor,» [Online]. Available: https://pulsesensor.com/blogs/news/6326816-anatomy-of-the-diy-heart-rate-monitor.
[10] «Pulsesensor,» [Online]. Available: https://pulsesensor.com/pages/code-and-guide.
[11] «Instructables - Pulse sensor,» [Online]. Available: https://www.instructables.com/circuits/howto/pulse+sensor/.
[12] «NRF24L01,» [Online]. Available: https://components101.com/wireless/nrf24l01-pinout-featuresdatasheet.
[13] Makerguides.com, «Arduino Nano pinout,» [Online]. Available: https://www.makerguides.com/arduinonano/.
[14] «LCD Custom Generator,» [Online]. Available: https://maxpromer.github.io/LCD-Character-Creator/.
[15] «MIT App Inventor,» [Online]. Available: https://appinventor.mit.edu/.
[16] M. Alessandro, «Tempcontrol,» [Online]. Available: https://github.com/mastroalex/tempcontrol.
[17] «Highcharts,» [Online]. Available: https://www.highcharts.com/blog/products/highcharts/.
[18] randomnerdtutorials.com, «ESP8266 Pinout Reference: Which GPIO pins should you use?,» [Online]. Available: https://randomnerdtutorials.com/esp8266-pinout-reference-gpios/.
[19] Wikipedia, «HTTP POST,» [Online]. Available: https://en.wikipedia.org/wiki/POST_(HTTP).
[20] mrw.it, «Pagina protetta da password,» [Online]. Available: https://www.mrw.it/php/pagina-protettapassword_11675.html.
[21] Sparkfun, «MyoWare Muscle Sensor,» [Online]. Available: https://www.sparkfun.com/products/13723.

## Indice delle figure

Fig. 2 – Esempio di struttura realizzata con gli ingranaggi, plastica sagomata e una base di alluminio

Fig. 15 – Segnale smoothed (blu), segnale originale (verde), soglia (rosso). Quando il segnale è al di sotto del valore soglia l’arto è rilassato, mentre, quando il segnale è al di sopra della soglia il muscolo è contratto.........8 (https://d.docs.live.net/83c81f65cfd2a4cc/Desktop/codici%20completi/Relazione%20finale2.docx)

Fig. 17 – Immagine del sensore. Il cavo rosso corrisponde ai 5V, il cavo nero al GND e il cavo viola è il

Fig. 28 – Arduino Uno con i servo, il convertitore di livello logico, il modulo NRF24 e il modulo bluetooth....14 (https://d.docs.live.net/83c81f65cfd2a4cc/Desktop/codici%20completi/Relazione%20finale2.docx)

## Appendice

Appendice A

Appendice A

Appendice B

Appendice B

Appendice C

Appendice C

Appendice D

Appendice D

Appendice E

Appendice E

Appendice F


Appendice F

Appendice G

Appendice G

Appendice H

Appendice H

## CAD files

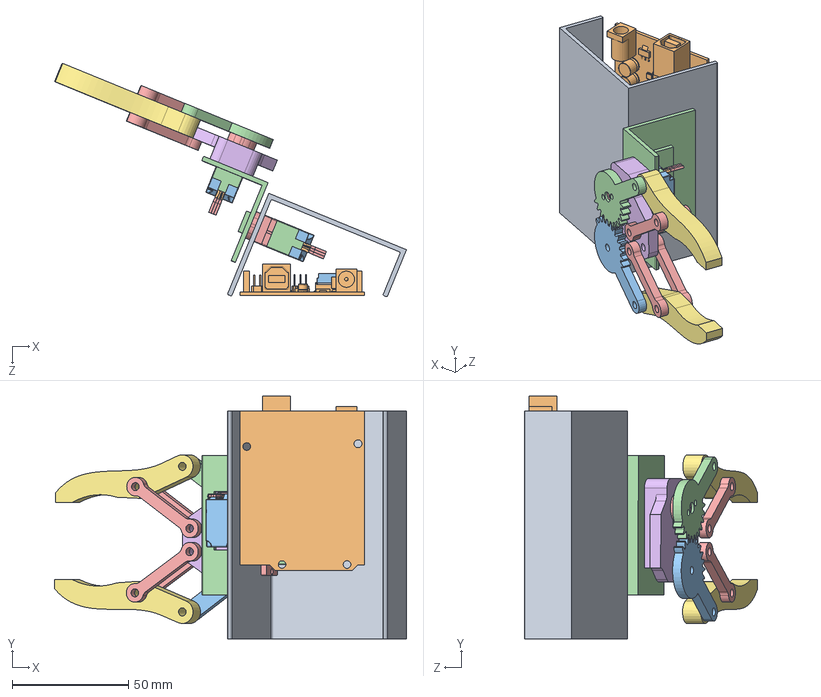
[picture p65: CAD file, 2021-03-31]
extra/cad/cad finale.SLDASM
151.4 x 104.5 x 100.4 mm
base
atmel
Parte2^cad finale
PCB x 2
smdChip8pin x 4
1.7mmSmdCeramicCapacitor x 4
smdceramiccapacitor x 4
tinySMDResistor x 4
tinyVoltageRegulator x 2
solder x 6
solder1.8 x 6
GearTop x 2
Gear3 x 2
Gear2 x 2
Gear4 x 2
Gear5 x 2
MiddleShaft x 2
BottomBody x 2
MiddleBody x 2
UpperBody x 2
microBrushedMotor x 2
verticalTrimmerPot x 2
TinyScrew x 4
Sticker x 4
PCB-shortwires x 2
gear1_r1
gear2_r1
grip link 1_r1 x 4
Gripper base_r1
Gripper 1_r1 x 2

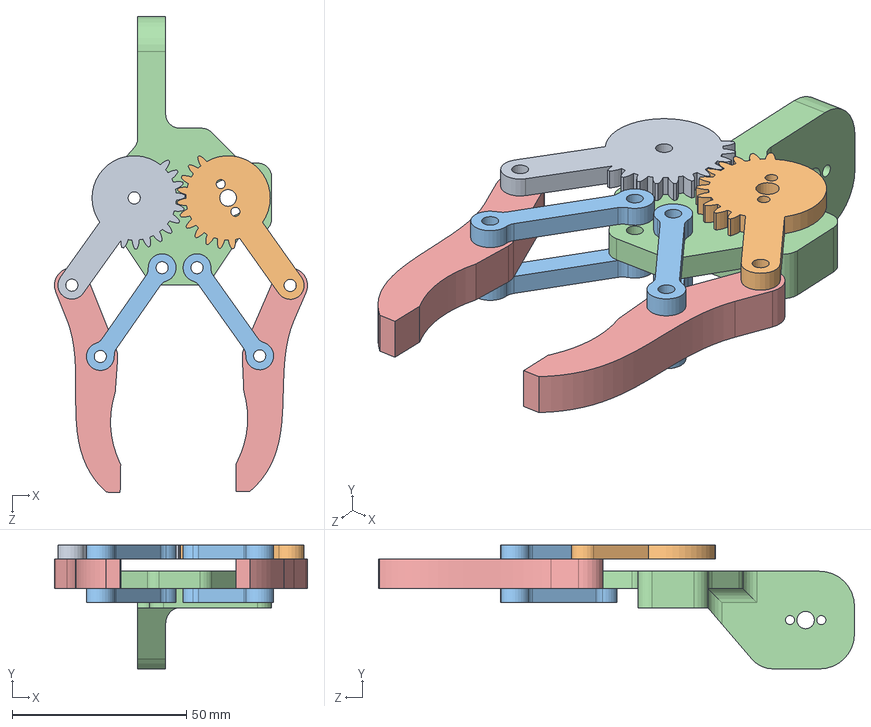
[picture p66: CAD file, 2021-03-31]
extra/cad/cad extra file/Gripper Assembly.SLDASM
72.5 x 35.5 x 136.4 mm
gear1
Gear2
grip link 1 x 4
Gripper base
Gripper 1 x 2

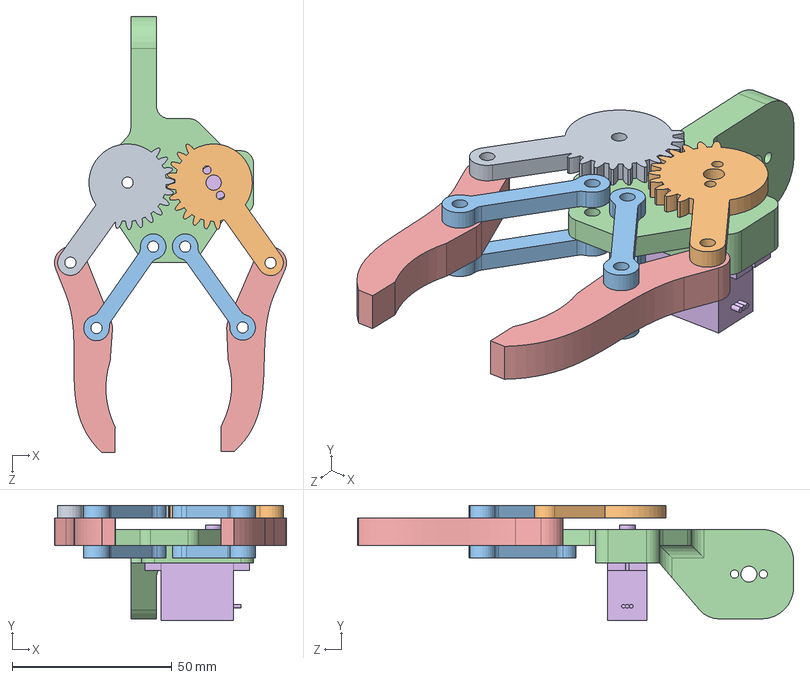
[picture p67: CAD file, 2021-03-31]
extra/cad/cad extra file/Gripper/Gripper Assembly.SLDASM
72.5 x 36.0 x 136.4 mm
gear1
gear2
grip link 1 x 4
Gripper base
Gripper 1 x 2
Servo Motor Micro 9g

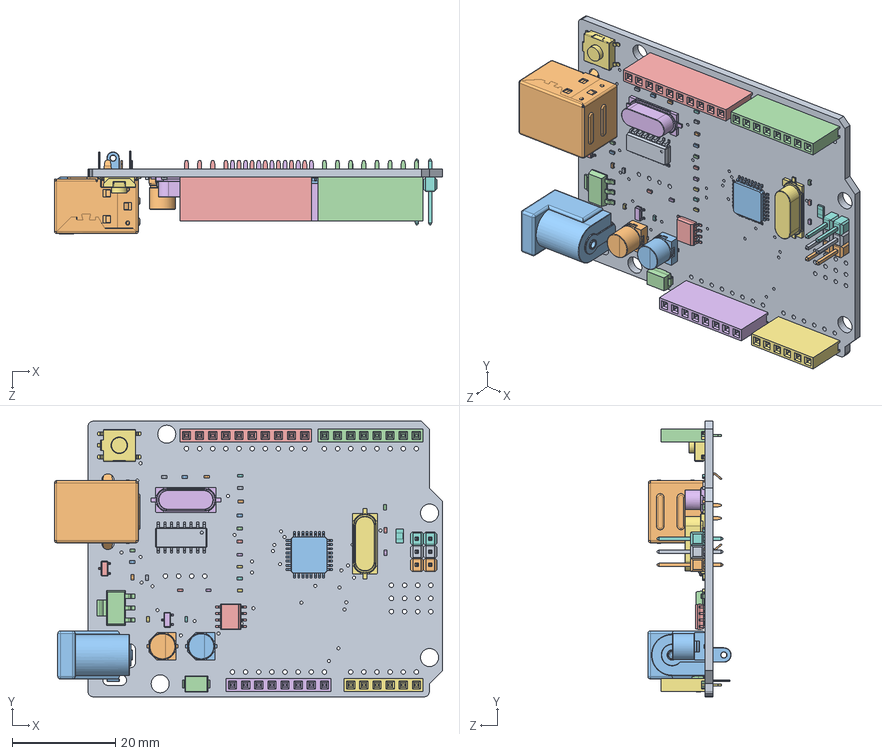
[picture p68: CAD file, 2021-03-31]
extra/cad/cad extra file/Arduino UNO Rev.3 (CH340)-CAWEB.ORG.stp.SLDASM
75.0 x 53.3 x 16.1 mm
PCB.stp
USB-B.stp
DC_Jack.stp
Header female 8.stp
Header female 10.stp
Header female 8 (2).stp
Header female 6.stp
Header male 2.stp
Header male 2 (2).stp
Header male 2 (3).stp
Atmega328p-AU.stp
Diode.stp
LM358.stp
16MHZ Crystal.stp
16MHZ Crystal (2).stp
0603 Package.stp
0603 Package (2).stp
0603 Package (3).stp
0603 Package (4).stp
0603 Package (5).stp
0603 Package (6).stp
0603 Package (7).stp
0603 Package (8).stp
R1.stp
0603 Package (24).stp
0603 Package (23).stp
0603 Package (22).stp
0603 Package (21).stp
0603 Package (20).stp
0603 Package (19).stp
0603 Package (18).stp
0603 Package (17).stp
0603 Package (16).stp
0603 Package (15).stp
0603 Package (14).stp
0603 Package (13).stp
0603 Package (12).stp
0603 Package (11).stp
0603 Package (10).stp
0603 Package (9).stp
CH340G.stp
47uF 27v cap.stp
47uF 27v cap (2).stp
LM1117.stp
Transistor SOC Package.stp
Transistor SOC Package (2).stp
A sexy yellow button.stp

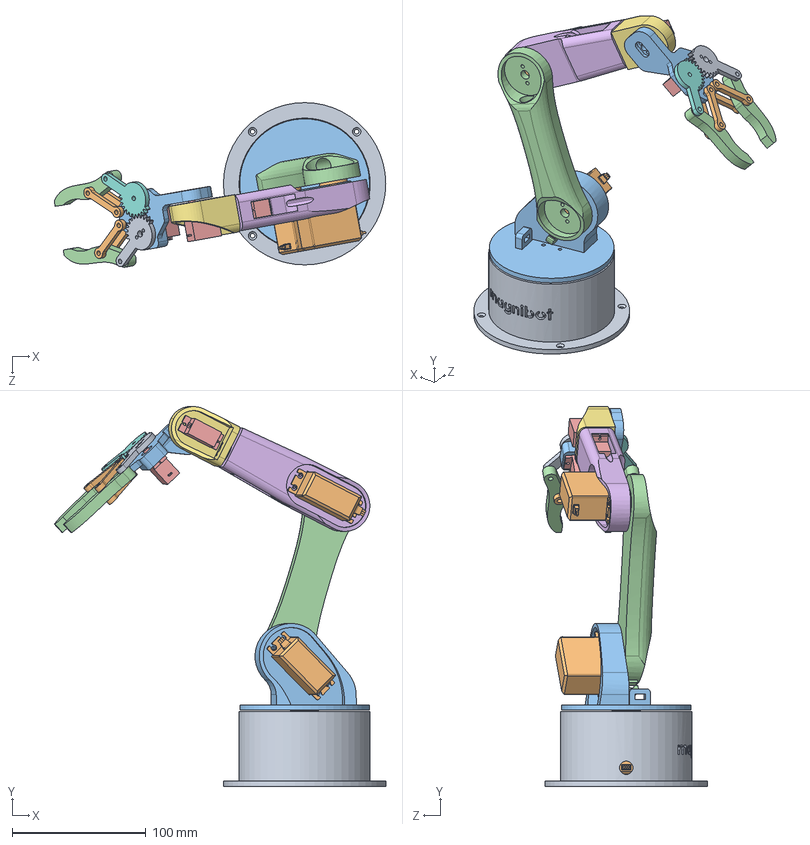
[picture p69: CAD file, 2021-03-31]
extra/cad/cad extra file/Robot Arm magnibot 3D Model/Robotic Arm.SLDASM
247.7 x 283.9 x 123.1 mm
Base
Servo Motor MG996R x 3
Waist
Arm 01
Servo Motor Micro 9g x 3
Arm 02 v3
Arm 03
gear1
gear2
grip link 1 x 4
Gripper base
Gripper 1 x 2

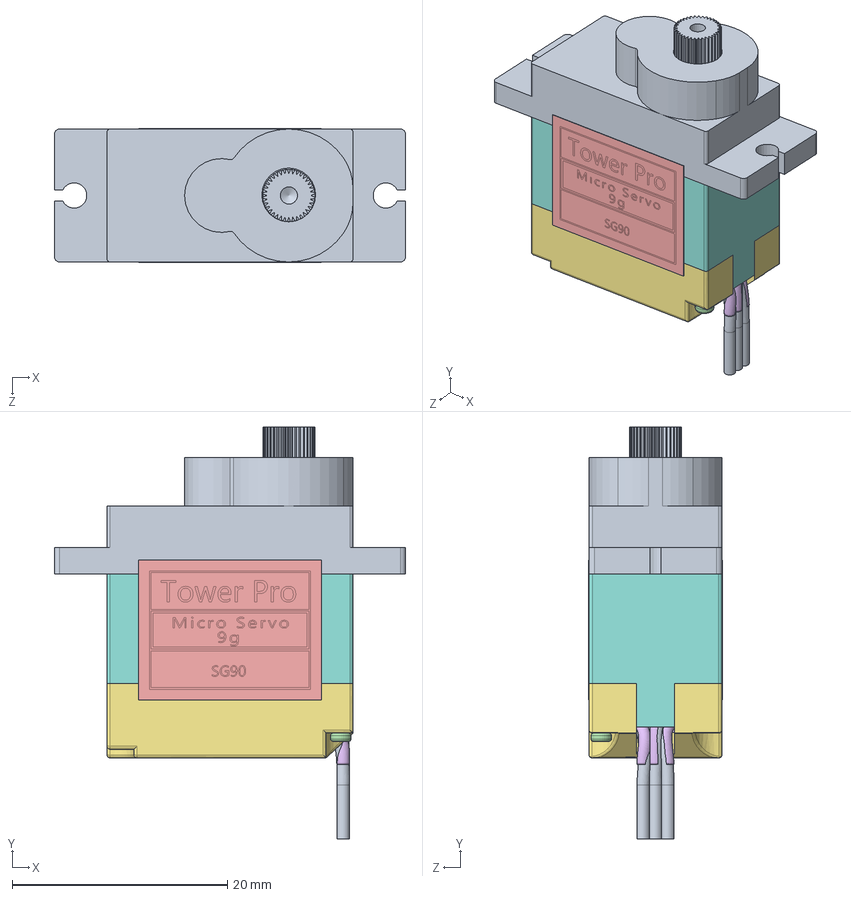
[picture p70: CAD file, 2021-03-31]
extra/cad/cad extra file/SG90ServoMotor.SLDASM
32.7 x 38.3 x 12.4 mm
PCB
smdChip8pin x 2
1.7mmSmdCeramicCapacitor x 2
smdceramiccapacitor x 2
tinySMDResistor x 2
tinyVoltageRegulator
solder x 3
solder1.8 x 3
GearTop
Gear3
Gear2
Gear4
Gear5
MiddleShaft
BottomBody
MiddleBody
UpperBody
microBrushedMotor
verticalTrimmerPot
TinyScrew x 2
Sticker x 2
PCB-shortwires

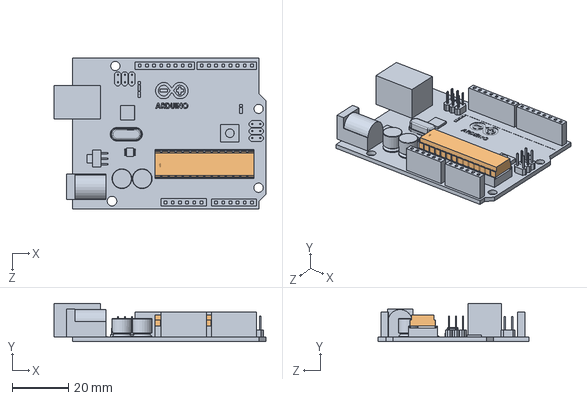
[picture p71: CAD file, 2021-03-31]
extra/cad/cad extra file/srduino.SLDASM
75.1 x 13.6 x 53.5 mm
atmel

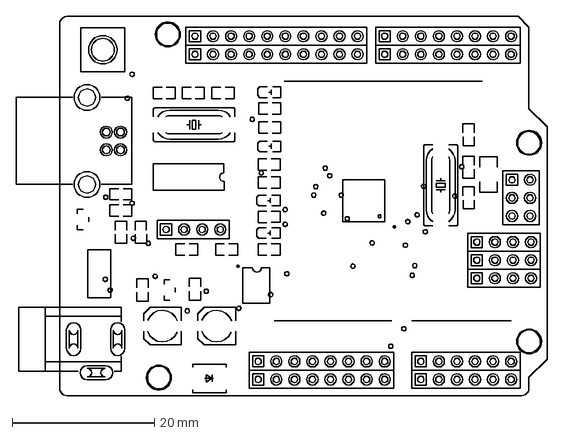
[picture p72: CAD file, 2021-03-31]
extra/cad/cad extra file/arduino-uno-rev-3-ch340-1.snapshot.23/PCB files/Arduino UNO Rev.3 (CH340)-CAWEB.ORG.dxf
74.7 x 53.3 mm

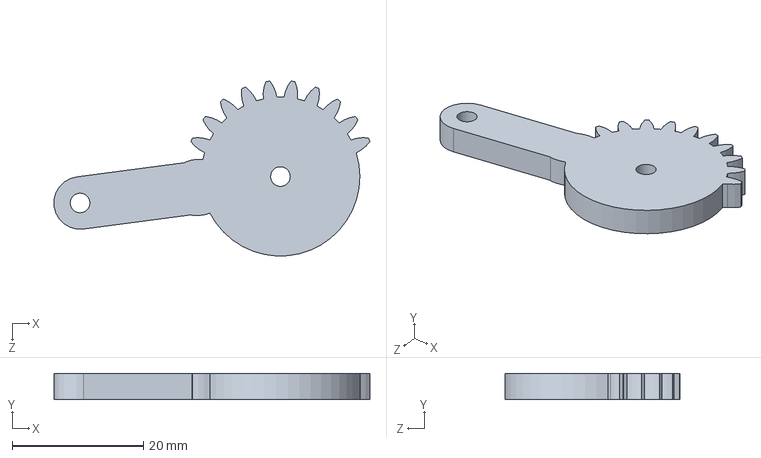
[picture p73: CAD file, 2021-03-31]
extra/cad/cad extra file/Gripper/gear2.SLDPRT
48.1 x 4.00 x 26.6 mm

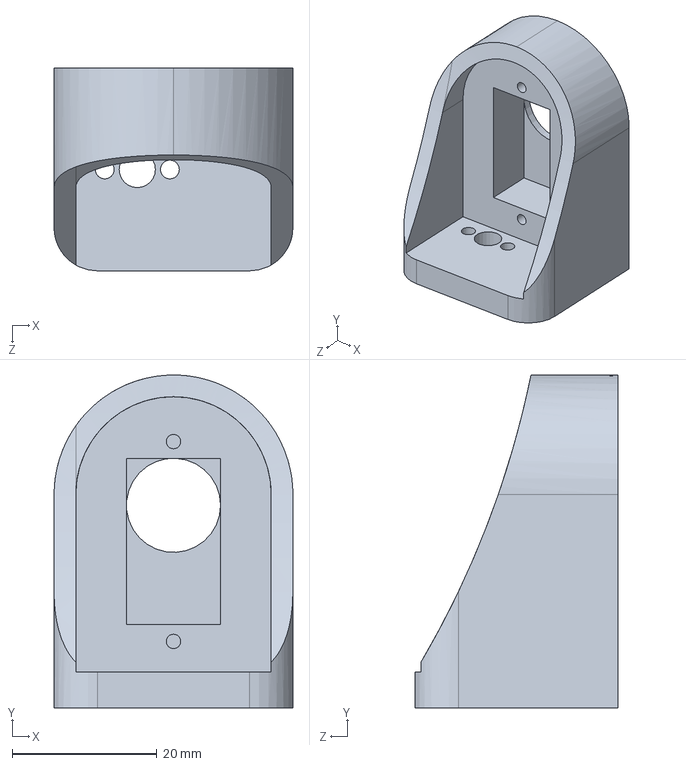
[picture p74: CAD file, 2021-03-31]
extra/cad/cad extra file/Robot Arm magnibot 3D Model/Arm 03_r1.SLDPRT
33.0 x 46.0 x 28.0 mm

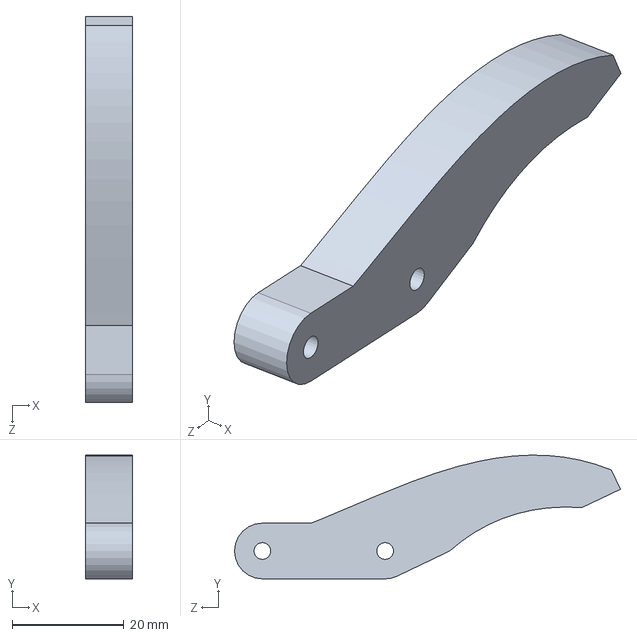
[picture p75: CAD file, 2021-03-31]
extra/cad/cad extra file/Robot Arm magnibot 3D Model/Gripper/Gripper 1_r1.SLDPRT
8.50 x 22.2 x 69.2 mm

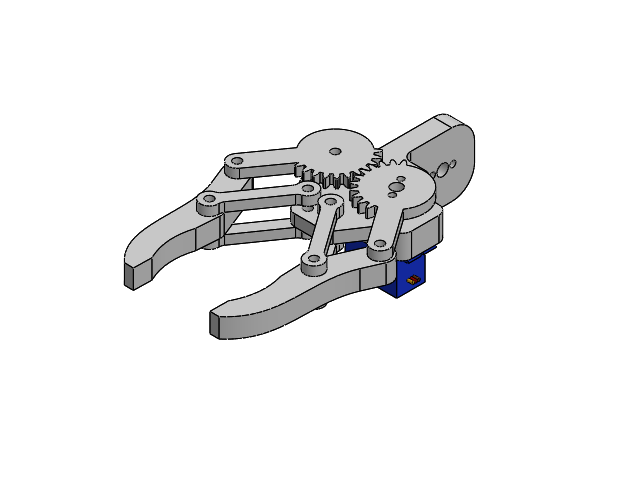
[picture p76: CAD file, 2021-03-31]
extra/cad/cad extra file/Robot Arm magnibot 3D Model/Gripper/Gripper Assembly_r1.SLDASM
gear1_r1
gear2_r1
grip link 1_r1 x 4
Gripper base_r1
Gripper 1_r1 x 2
Servo Motor Micro 9g_r1

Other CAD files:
extra/cad/cad extra file/Robot Arm magnibot 3D Model/Gripper/Gripper Assembly.SLDASM
extra/cad/cad extra file/Gripper Assembly_r1.SLDASM
extra/cad/cad extra file/PCB.SLDASM
extra/cad/cad extra file/GearSet.SLDASM
extra/cad/cad extra file/MiddleBody.SLDPRT
extra/cad/cad extra file/1.7mmSmdCeramicCapacitor.SLDPRT
extra/cad/cad extra file/BottomBody.SLDPRT
extra/cad/cad extra file/Gear2.SLDPRT
extra/cad/cad extra file/Gear3.SLDPRT
extra/cad/cad extra file/Gear4.SLDPRT
extra/cad/cad extra file/Gear5.SLDPRT
extra/cad/cad extra file/GearTop.SLDPRT
extra/cad/cad extra file/Gripper/Gripper 1 v2.SLDPRT
extra/cad/cad extra file/Gripper/Gripper 1.SLDPRT
extra/cad/cad extra file/Gripper/Gripper 1_r1.SLDPRT
extra/cad/cad extra file/Gripper/Gripper base.SLDPRT
extra/cad/cad extra file/Gripper/Gripper base_r1.SLDPRT
extra/cad/cad extra file/Gripper/gear1.SLDPRT
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

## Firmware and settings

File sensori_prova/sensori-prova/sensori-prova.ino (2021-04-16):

#include <MPU6050_tockn.h>
#include <Wire.h>
#include <Servo.h>


Servo servomotor; // inizializziamo il servo
Servo servopinza;

const int pinzapin = 3; // pin servo per la pinza


float tempmpu = 0; // temperatura MPU5060
float angle = 0;  //angolo lungo z MPU5060
int t1 = 0; // timer per la stampa dei valori
int pausa = 400 ; // pausa per il serial print
const int servopin = 9; // pin per il servo
const int angolopolso = 75; // definiamo l'angolo di massima rotazione del polso per la funzione map
const int angolorotservo = 150; // angolo di massima rotazione laterale
const int angolominservo = 3; // angolo minimo del servo
int pos = 0; // poszione servo

int bottone = 7;

MPU6050 mpu6050(Wire);

// emg


int EMG_pin = A0;


#define pinzamin 50
#define pinzamax 100

int somma = 0;
int value = 0;


// smoothing


const int numReadings = 50;

int readings[numReadings];      // the readings from the analog input
int readIndex = 0;              // the index of the current reading
int total = 0;                  // the running total
int average = 0;                // the average

// threeshold controll

long t3 = 0; // contator for controll cycle
long t4 = 20; // pause time for controll cycle
boolean controllo[10]; // vec for controll cycle
boolean stato; // boolean variable fro controll cycle
int i = 0;
int soglia = 300; // valore di soglia per la chiusura della pinza


void setup() {
  Serial.begin(9600);
  Wire.begin(); // avvio e inizializzo il gyro

  mpu6050.begin();
// mpu6050.calcGyroOffsets(true);
  mpu6050.setGyroOffsets(0, 0, 0);

  servopinza.attach(pinzapin); // servo pinza
  servomotor.attach(servopin); // servo sul pin servopin

  // initialize all the readings to 0:
  for (int thisReading = 0; thisReading < numReadings; thisReading++) {
    readings[thisReading] = 0;
  }

  t1 = millis();
//  pinMode(bottone, INPUT);
}



void loop() {

  //  emg reading and smoothing
  // subtract the last reading:
  total = total - readings[readIndex];
  // read from the sensor:
  readings[readIndex] = analogRead(EMG_pin);
  // add the reading to the total:
  total = total + readings[readIndex];
  // advance to the next position in the array:
  readIndex = readIndex + 1;

  // if we're at the end of the array...
  if (readIndex >= numReadings) {
    // ...wrap around to the beginning:
    readIndex = 0;
  }

  // calculate the average:
  average = total / numReadings;


  mpu6050.update();
  tempmpu = mpu6050.getTemp(); // prende la temperatura

  angle = mpu6050.getAngleZ(); // prende l'angolo lungo x

  pos = map((int)angle, -angolopolso, angolopolso, 0, 180); // mappiamo la funzione dai valori letti dall IMU nel range del servo

  if (millis() > 1000 ) { // mettiamo un blocco al motore nel mentre che IMU fa la calibrazione
    servomotor.write(pos);
  }


  if (millis() - t1 > pausa) {
    Serial.print("anglez : ");
    Serial.print(angle);
    Serial.print("\t temp : ");
    Serial.println(tempmpu);
    Serial.print("Average: ");
    Serial.print(average);
    Serial.print(", Soglia: ");
    Serial.print(soglia);
    Serial.print(", EMG: ");
    Serial.println(analogRead(EMG_pin));
    t1 = millis();
  }


  // closing or opening calmp
  if (average > soglia) {

    servopinza.write(pinzamax);// chiudo la pinza
  }
  if (millis() - t3 < t4) {
    if (average < soglia) {
      controllo[i] = LOW;
    }
    else {
      controllo[i] = HIGH;
    }
    if (i < 10) {
      i++;
    }
    t3 = millis();
  }

  for (int j = 0; j < 10; j++) {
    if (controllo[j] == LOW) {
      stato = LOW;
    }
    else {
      stato = HIGH;
    }
  }
  if (stato == LOW) {
    servopinza.write(pinzamin);// apriamo la pinza
  }

  delay(1);

}

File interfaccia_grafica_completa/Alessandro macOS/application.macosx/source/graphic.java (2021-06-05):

import processing.core.*; 
import processing.data.*; 
import processing.event.*; 
import processing.opengl.*; 

import controlP5.*; 
import processing.serial.*; 

import java.util.HashMap; 
import java.util.ArrayList; 
import java.io.File; 
import java.io.BufferedReader; 
import java.io.PrintWriter; 
import java.io.InputStream; 
import java.io.OutputStream; 
import java.io.IOException; 

public class graphic extends PApplet {


ControlP5 cp5;

Serial MyPort;

float target1;
float target2;
PFont font24;
PFont font12;

boolean pulsante=false;

//dati comunicazione
float tempC = 0;
float Incl = 0;
float Batt=0;
float[] data; 


Termom termom= new Termom(); 
Schermo schermo=new Schermo();
Slider slider=new Slider();
Serialcomunication serialcomunication=new Serialcomunication();
Switchcommand switchcommand = new Switchcommand();
Grafico grafico = new Grafico();

public void setup()
{
  
  background(255);

  MyPort =  new Serial(this, "/dev/tty.HC-05-SerialPort", 9600);
  //MyPort.bufferUntil('\n');
  grafico.setdati();
  cp5 = new ControlP5(this);
  switchcommand.setup();
  schermo.cuore(); // inizializza l'immagine del cuore 
  slider.sliderset();
}

public void draw()
{
  //Grafico
  background(255);
  serialcomunication.serialreceive();
  grafico.assi();
  termom.disegna();
  slider.slider1();
  slider.slider2();
  schermo.temperaturadigitale(tempC);
  schermo.inclinazione(Incl);
  schermo.battito(Batt);
  serialcomunication.serialsend();
}

//icon controll
public void icon(boolean theValue) {

  println("got an event for icon", theValue);
  if (theValue == true) {
    MyPort.write("C1");
    pulsante=true;
  }  
  if (theValue == false) {
    MyPort.write("C0");
    pulsante=false;
  }
} 
public class Grafico {
public float[] datax; 
 public Grafico(){}
 
 public void setdati(){
 data = new float[1000];
  for (int i=0; i < data.length; i++) {
    data[i] = 100;
  }
  datax = new float[data.length];
  for (int i=0; i < datax.length; i++) {
    float passo=900/PApplet.parseFloat(data.length);
    datax[i] = 50+i*passo;
  }
 }
 
 public void assi(){
 for (int i=0; i<data.length-1; i++) {
    fill(55, 200, 50);
    line(datax[i], 650-data[i], datax[i+1], 650-data[i+1]);
  }


  stroke(0, 0, 250);
  strokeWeight(2);
  //line(50,800-V,950,800-V);
  stroke(0, 0, 0);
  line(50, 350, 50, 650);
  line(50, 650, 950, 650);
  fill(0, 0, 0);
  triangle(48, 350, 52, 350, 50, 340);
  triangle(940, 648, 940, 652, 950, 650);
  textSize(12);
  text("t(s)", 965, 665);
  text("V(v)", 15, 350);
 }
}
public class Schermo {
  float tempC = 0;
  float Incl = 0;
  float Batt=0; 
PImage battitook;
int  graycol=130, xshift=4, yshift=50;
  int x1=50, y1=50;




  public Schermo() {
  }
  public void cuore(){
        battitook = loadImage("battitook.png");

  }

  public void temperaturadigitale(float tempC) {
    // Rettangolo dati 
    fill(190);
    stroke(0);
    strokeWeight(1);
    rect(1200, 70, 180, 140, 7);
    fill(0, 0, 0);
    textFont(font24);
    textAlign(LEFT);
    text("Temperature", 1210, 40);
    text(" °C", 1300, 150);
    text(nfc(tempC, 1), 1250, 150);
  }

  public void inclinazione(float Incl) {

    //Rettangolo inclinazione
    fill(190);
    stroke(0);
    strokeWeight(1);
    rect(700, 70, 180, 140, 7);
    fill(0, 0, 0);
    textFont(font24);
    text("Roll", 760, 40);
    text(" °", 800, 150);
    text(nfc(Incl, 1), 770, 150);
  }
  
  public void battito (float Batt){
    //Battito
  textFont(font24); 
  fill(250, 0, 0); 
  text("BPM", x1+xshift+950, y1-10); 
  fill(0, 0, 0);
  image(battitook, x1+900, y1+20);
  text(nfc(Batt, 0), 1017, 150);
  }
}
public class Serialcomunication extends Grafico {
  String dati = " ";
  String valore="";
  char dativec; 
  int index = 0;
  public long ti=0; 
public long ti2=0; 



 int y2=95, y4=245;
  public Serialcomunication() {
  }

  public void serialsend() {
    if (mousePressed) {
      if (millis()-ti>500) {
        if (pulsante==true) {
          if (mousePressed && mouseY < y2+20) {
            float pinzamap=map(target1, 50, 350, 0, 180);
            String pinza="P"+str(pinzamap);
            MyPort.write(pinza);
            println(pinza);
          }
        }

        ti=millis();
      }
      if (millis()-ti2>500) {
        if (pulsante==true) {
          if (mousePressed && mouseY > y4-20) {
            float rotazmap=map(target2, 50, 350, -90, 90);
            String rotaz="R"+ str(rotazmap);
            MyPort.write(rotaz);
            println(rotaz);
          }
        }
        ti2=millis();
      }
      //println(rotaz);
    }
  }

  public void serialreceive() {
    if (MyPort.available() > 0) {
      dati = MyPort.readStringUntil('\n');
      dati=dati.trim();
    }
    //  println(dati);
    dativec=dati.charAt(0);

    if (dativec == 'T') {
      //   print("Temperature: ");
      valore = "";
      for (int i = 1; i < dati.length(); i++) {
        valore = valore +dati.charAt(i) ;
      }
      tempC = PApplet.parseFloat(valore);
      //   println(tempC);
    }

    if (dativec == 'A') {
      //   print("Angle: ");
      valore = "";
      for (int i = 1; i < dati.length(); i++) {
        valore = valore +dati.charAt(i) ;
      }
      Incl = PApplet.parseFloat(valore);
      //   println(Incl);
    }
    if (dativec == 'B') {
      //    print("BPM: ");
      valore = "";
      for (int i = 1; i < dati.length(); i++) {
        valore = valore +dati.charAt(i) ;
      }
      Batt = PApplet.parseFloat(valore);
      //   println(Batt);
    }
    if (dativec == 'M') {
      //   print("average: ");
      valore = "";
      for (int i = 1; i < dati.length(); i++) {
        valore = valore +dati.charAt(i) ;
      }
      if (PApplet.parseInt(valore)<0) {
        valore="1023";
      }
      if (index<data.length) {
        //data[index]=float(valore);
        data[index]=map(PApplet.parseFloat(valore), 0, 1024, 0, 300);
        index++;
      } else if (index==data.length) {
        index=0;
        data[index]=map(PApplet.parseFloat(valore), 0, 1024, 0, 300);
      }
      //  println(valore) ;
      // println(datax);
    }
  }
}
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

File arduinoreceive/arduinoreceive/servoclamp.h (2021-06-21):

#ifndef servoclamp
#define servoclamp

#include <Servo.h>

#include "rotation.h"

Servo servopinza;

const int pinzapin = 3; // pin servo per la pinza

int soglia ;
int average;
boolean controllo[10]; // vec for controll cycle
boolean stato; // boolean variable fro controll cycle
int i = 0;

unsigned long t3 = 0; // contator for controll cycle
unsigned long t4 = 20; // pause time for controll cycle

#define pinzamin 80
#define pinzamax 110

void pinzacontrol (int soglia) {
  // closing or opening calmp
  if (average > soglia) {

    servopinza.write(pinzamax);// chiudo la pinza
  }
  if (millis() - t3 > t4) {
    if (average < soglia) {
      controllo[i] = LOW;
    }
    else {
      controllo[i] = HIGH;
    }
    if (i < 10) {
      i++;
    }
    else if (i = 10) {
      i = 0;
    }
    t3 = millis();
  }

  for (int j = 0; j < 10; j++) {
    if (controllo[j] == LOW) {
      stato = LOW;
    }
    else {
      stato = HIGH;
    }
  }
  if (stato == LOW) {
    servopinza.write(pinzamin);// apriamo la pinza
  }
}


void pinzacontrol2 (int angolo_pinza) {
  // closing or opening calmp
  int angolo_pinza_map = map(angolo_pinza, 0, 180, pinzamin, pinzamax);

  servopinza.write(angolo_pinza_map);// chiudo la pinza
}


#endif

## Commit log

2021-03-31 file per cad
    [1.7mmSmdCeramicCapacitor.SLDPRT, Arduino UNO Rev.3 (CH340)-CAWEB.ORG.dxf, Arduino UNO Rev.3 (CH340)-CAWEB.ORG.f3d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]
2021-05-03 Revert "Merge branch 'main' of https://github.com/mastroalex/progelettronica into main"
    This reverts commit 9cd2a24e451d502446bc0865e7002b4682b24ec3, reversing
    changes made to c11a5e592682f4910ba0de375183d0e51306a951.
    [esp8266_schema.fzz]
2021-05-03 Revert "Revert "Merge branch 'main' of https://github.com/mastroalex/progelettronica into main""
    This reverts commit feb42bbe24b3fbffc40481ad50cba602b64597c0.
    [esp8266_schema.fzz]
2021-06-22 Arduinosense correct
